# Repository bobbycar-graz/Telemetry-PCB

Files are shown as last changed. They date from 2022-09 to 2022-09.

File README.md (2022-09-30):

# Bobby-Car Telemetry PCB

This board should be mounted on the Bobby-Car.

There are 2 CAN bus connectors, pin-compatible with the boardcomputer PCB, and can either be wired:
- after the boardcomputer or
- in-line between the motorcontrollers and the boardcomputer

### Hardware Features
- SN65HVD230 CAN transceiver
- ESP32-WROOM-32E (8MB)
- CH343G USB to UART converter for programming
- ATGM336H-5N31 GNSS
  - supports GPS (US), GLONASS (Russia), Galileo (EU), BeiDou (China), QZSS (Japan)
  - u.FL connector for active antenna 
  - protocol compatible with NEO-6M
  - optional 3V rechargeable battery for fast cold start
- self bomb microSD card slot
- LM75B temperature sensor
- RA-01SH 868MHz LoRa module with two antenna options:
  - integrated u.FL connector for external helical antenna
  - solder jumper to enable the onboard PCB helical antenna
- TPMP2359DJ DC-DC converter (up to 30V input, 3.3V output), so board can be powered by:
  - USB-C connector (5V) or
  - CAN bus (12V-15V)
- TTL UART receive to receive log messages from the boardcomputer

### Use cases
- Acquire data with onboard sensors and send it to the boardcomputer
  - GPS/GNSS time, position, speed, heading
  - temperature
- Log data to the microSD card:
   - GPS and temperature data
   - CAN BUS messages
   - LoRa messages
   - ESP-NOW messages
   - GPS-mapped Wi-Fi scan results
   - UART log messages from the boardcomputer
- GPS geofencing (slowdown/stop, notification to other Bobby-Cars)
- Calibrate wheel circumference by comparing GPS speed with wheel speed
- Send GPS position over LoRa so that:
  - other Bobby-Cars can show nearby Bobby-Cars on a radar display
  - the Bobby-Car can be tracked on a map in case of loss or theft
- Control actuators such as door openers, lights, etc. over LoRa
- Receive LoRa messages from environmental sensors such as weather stations, air quality sensors, etc.
- Send ESP-NOW beacons with the current UTC time to other Bobby-Cars that lack a GNSS receiver
- Upload microSD card data to a cloud service automatically when connected to a Wi-Fi network

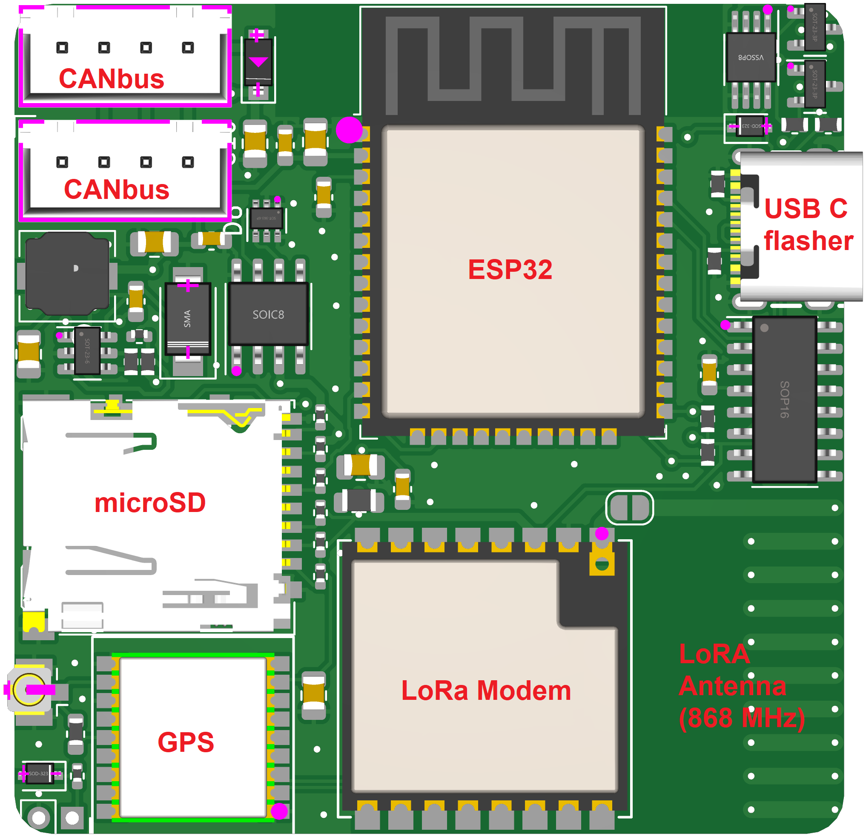
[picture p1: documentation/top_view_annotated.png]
PCB image


### Compliance
- Compliant with RED Directive 2014/53/EU (Radio Equipment Directive)
- Wi-Fi 2.4GHz 802.11b/g/n certified by Wi-Fi Alliance
- FCC ID of ESP32-WROOM-32E: [2AC7Z-ESP32WROOM32E](https://fccid.io/2AC7Z-ESP32WROOM32E)
- Compliant with LVD Directive 2014/35/EU (Low Voltage Directive)
- Compliant with EMC standard EN 55032, EN 55024, EN 61000-6-2, EN 61000-6-4 (Class B)
- Compliant with RoHS Directive 2011/65/EU (Restriction of Hazardous Substances)
- Compliant with REACH Regulation (EC) No 1907/2006 (Registration, Evaluation, Authorisation and Restriction of Chemicals)
- Compliant with WEEE Directive 2012/19/EU (Waste Electrical and Electronic Equipment)
- Compliant with ELV Directive 2011/65/EU (End of Life Vehicle)
- Compliant with ISO 11898-1:2003 CAN bus physical layer and data link layer specifications

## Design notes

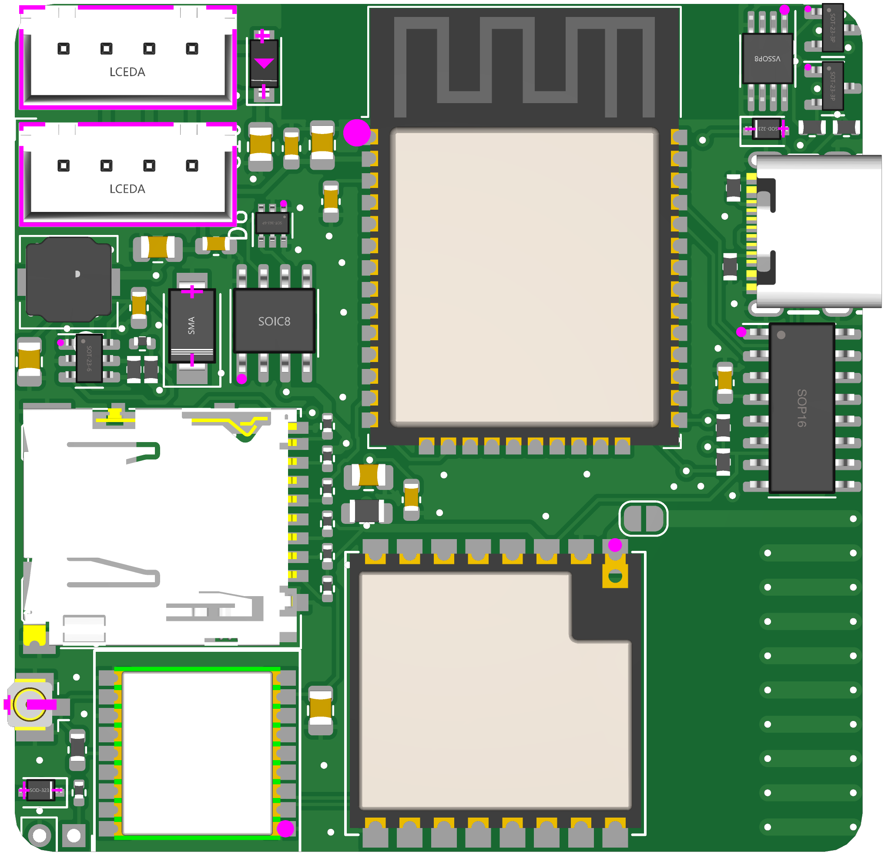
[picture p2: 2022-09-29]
documentation/top_view.png

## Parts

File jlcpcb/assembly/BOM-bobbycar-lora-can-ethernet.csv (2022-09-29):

Comment | Designator | Footprint | LCSC
bead | L2 | L_0805_2012Metric | C1017
Micro_SD_Card_Det_Hirose_DM3AT | J4 | microSD_HC_Hirose_DM3AT-SF-PEJM5 | C114218
SN65HVD231 | U6 | SOIC-8_3.9x4.9mm_P1.27mm | C12084
MC-311D | USBC1 | USB-C-SMD_MC-311D | C136423
Conn_01x04 | J1,J2 | JST_XH_B4B-XH-A_1x04_P2.50mm_Vertical | C144395
100n | C13,C3,C5,C6,C8 | C_0603_1608Metric | C14663
10uF | C1,C12,C4,C7 | C_0805_2012Metric | C15850
D_Schottky | D1,D2 | D_SOD-323 | C191023
1k | R15 | R_0402_1005Metric | C21190
SS8050_C2150 | Q1,Q2 | SOT-23 | C2150
B230A | D4 | D_SMA | C22452
12k | R10,R9 | R_0402_1005Metric | C22790
75k | R24 | R_0402_1005Metric | C23184
5k1 | R12,R8 | R_0402_1005Metric | C23186
470 | R1 | R_0402_1005Metric | C25117
24k | R25 | R_0402_1005Metric | C25769
47k | R16,R17,R18,R19,R20,R21 | R_0402_1005Metric | C25792
10k | R13,R14 | R_0402_1005Metric | C25804
Ai-Thinker-Ra-01SH | U2 | Ai-Thinker-Ra-01-LoRa | C2764087
LM75B | U3 | MSOP-8_3x3mm_P0.65mm | C2837470
CH343G | U5 | SOIC-16_3.9x9.9mm_P1.27mm | C2844153
MPM2359 | U7 | SOT-23-6 | C2959845
6.8nH | L1 | L_0603_1608Metric | C316305
4.7uH | L3 | L_Wuerth_HCI-5040 | C354606
10uF | C10,C9 | C_0805_2012Metric | C440198
10n | C11 | C_0603_1608Metric | C57112
ESP32-WROOM-32E | U1 | ESP32-WROOM-32 | C701342
D | D3 | D_SOD-123 | C8598
Antenna_Shield | AE1 | U.FL_Hirose_U.FL-R-SMT-1_Vertical | C88374
ATGM336H-5N31 | J3 | ATGM336H-5N31 | C90770
SP0505BAJT | D6 | SOT-363_SC-70-6 | SMF05CT1G
Battery_Cell | BT1 | PinSocket_1x02_P2.00mm_Vertical
Jumper_2_Open | JP1 | SolderJumper-2_P1.3mm_Open_RoundedPad1.0x1.5mm
Antenna | AE2 | Texas_SWRA416_868MHz_915MHz

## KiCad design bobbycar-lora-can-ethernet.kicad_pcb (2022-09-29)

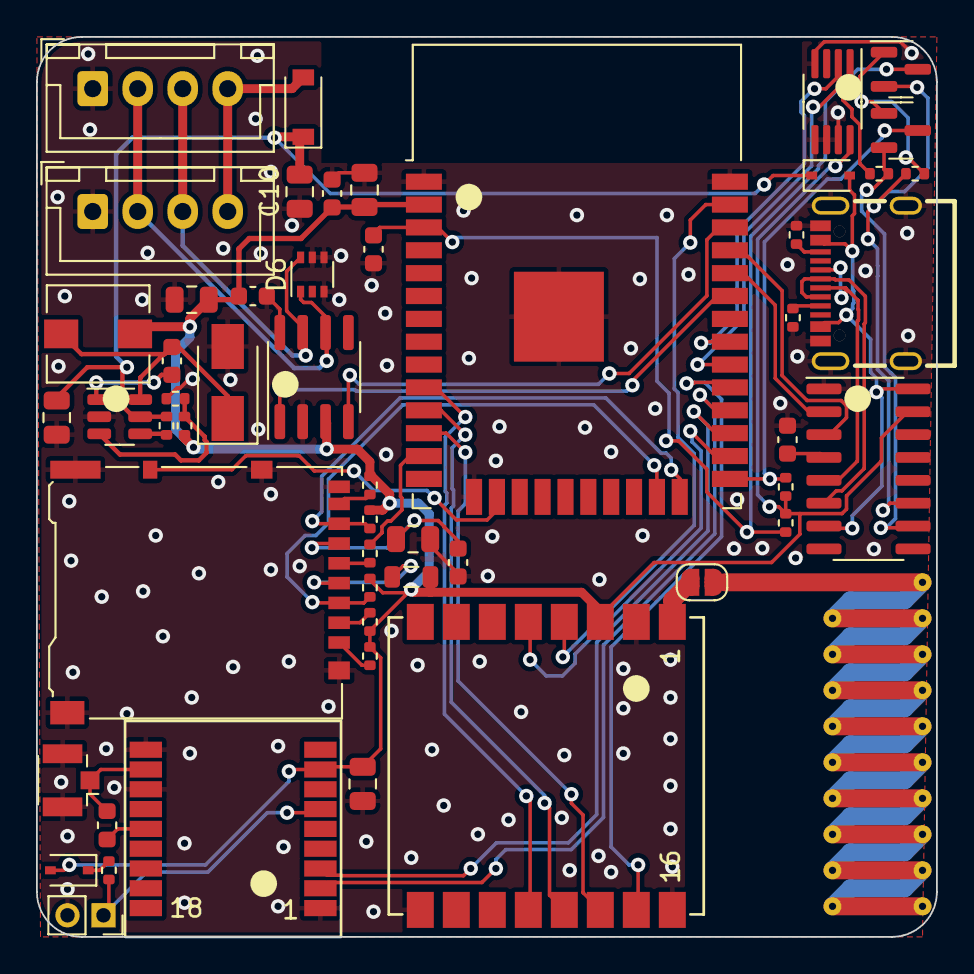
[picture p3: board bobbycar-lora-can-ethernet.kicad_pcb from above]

Board: 2 copper layers, 50.0 x 50.0 mm, 53 parts (0 on the bottom side), 52 nets.

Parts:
AE1: Antenna_Shield; U.FL_Hirose_U.FL-R-SMT-1_Vertical
AE2: Antenna; Texas_SWRA416_868MHz_915MHz
BT1: Battery_Cell; PinSocket_1x02_P2.00mm_Vertical
C1, C7, C9, C10, C12: 10uF; C_0805_2012Metric
C3, C5, C6, C8, C13: 100n; C_0603_1608Metric
C4: 10u; C_0805_2012Metric
C11: 10n; C_0603_1608Metric
D1, D2: D_Schottky; D_SOD-323
D3: D; D_SOD-123
D4: B230A; D_SMA
D6: SP0505BAJT; SOT-363_SC-70-6
J1, J2: Conn_01x04; JST_XH_B4B-XH-A_1x04_P2.50mm_Vertical
J3: ATGM336H-5N31
J4: Micro_SD_Card_Det_Hirose_DM3AT; microSD_HC_Hirose_DM3AT-SF-PEJM5
JP1: Jumper_2_Open; SolderJumper-2_P1.3mm_Open_RoundedPad1.0x1.5mm
L1: 6.8nH; L_0603_1608Metric
L2: bead; L_0805_2012Metric
L3: 4.7uH; L_Wuerth_HCI-5040
Q1, Q2: SS8050_C2150; SOT-23
R1: 470; R_0402_1005Metric
R8, R12: 5k1; R_0402_1005Metric
R9, R10: 12k; R_0402_1005Metric
R13, R14: 10k; R_0402_1005Metric
R15: 1k; R_0402_1005Metric
R16, R17, R18, R19, R20, R21: 47k; R_0402_1005Metric
R24: 75k; R_0402_1005Metric
R25: 24k; R_0402_1005Metric
U1: ESP32-WROOM-32E; ESP32-WROOM-32
U2: Ai-Thinker-Ra-01SH; Ai-Thinker-Ra-01-LoRa
U3: LM75B; MSOP-8_3x3mm_P0.65mm
U5: CH343G; SOIC-16_3.9x9.9mm_P1.27mm
U6: SN65HVD231; SOIC-8_3.9x4.9mm_P1.27mm
U7: MPM2359; SOT-23-6
USBC1: MC-311D; USB-C-SMD_MC-311D

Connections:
15V: C9.2, C10.2, D2.1 (K), D3.1 (K), R15.2, U7.5 (IN)
+3V3: C1.1, C4.2, C5.2, C8.1, C12.2, D1.2 (A), J3.8, L2.1, L3.2, R13.1, R14.2, R16.1, R17.1, R18.1, R20.1, R21.1, R24.2, U1.2 (VDD), U2.3 (VDD), U3.8 (+Vs), U5.15 (VIO), U6.3 (VCC)
+5V: D2.2 (A), U5.7 (VBUS), U5.16 (VDD5), USBC1.A4-B9 (VBUS), USBC1.B4-A9 (VBUS)
CANH: D6.6 (K), J1.3, J2.3, U6.7 (CANH)
CANL: D6.1 (K), J1.2, J2.2, U6.6 (CANL)
CAN_RX: U1.36 (IO22), U6.4 (R)
CAN_TX: U1.33 (IO21), U6.1 (D)
DTR: Q2.2 (E), R9.1, U5.10 (~DTR/TNOW)
EN: C13.2, Q1.3 (C), R13.2, U1.3 (EN)
ESP_RX: U1.34 (RXD0/IO3), U5.2 (TXD)
ESP_TX: U1.35 (TXD0/IO1), U5.3 (RXD)
GND: AE1.2 (Shield), BT1.2 (-), C1.2, C3.1, C4.1, C5.1, C6.1, C7.2, C8.2, C9.1, C10.1, C12.1, C13.1, D4.2 (A), D6.3 (K), D6.4 (K), D6.5 (K), J1.1, J2.1, J3.1, J3.10, J3.12, J4.9 (DET_B), J4.11 (SHIELD), R8.2, R12.1, R25.1, U1.1 (GND), U1.15 (GND), U1.38 (GND), U1.39 (GND), U2.2 (GND), U2.9 (GND), U2.16 (GND), U3.4 (GND), U3.5 (A2), U3.6 (A1), U3.7 (A0), U5.1 (GND), U6.2 (GND), U6.8 (Rs), U7.2 (GND), USBC1.1 (SHIELD), USBC1.2 (SHIELD), USBC1.3 (SHIELD), USBC1.4 (SHIELD), USBC1.A1-B12 (GND), USBC1.B1-A12 (GND)
GPIO2_SD_DAT0: J4.7 (DAT0), R20.2, U1.24 (IO2)
GPIO14_SD_CLK: R19.1, U1.13 (IO14)
GPIO15_SD_CMD: J4.3 (CMD), R18.2, U1.23 (IO15)
GPS_RX: J3.3, U1.27 (IO16)
GPS_TX: J3.2, U1.28 (IO17)
I2S_SCL: U1.31 (IO19), U3.2 (SCL)
I2S_SDA: U1.30 (IO18), U3.1 (SDA)
IO0: Q2.3 (C), R14.1, U1.25 (IO0)
LORA_CLK: U1.10 (IO25), U2.12 (SCK)
LORA_MISO: U1.11 (IO26), U2.13 (MISO)
LORA_MOSI: U1.12 (IO27), U2.14 (MOSI)
LORA_NSS: U1.29 (IO5), U2.15 (~NSS)
LORA_RESET: U1.37 (IO23), U2.4 (~RESET)
LORA_TX_EN: U1.26 (IO4), U2.5 (DIO0)
unnamed: AE1.1 (A), J3.11, L1.1
unnamed: AE2.1 (A), JP1.2 (B)
unnamed: C3.2, U5.4 (V3)
unnamed: C6.2, C7.1, J4.6 (VSS)
unnamed: C11.1, D4.1 (K), L3.1, U7.6 (SW)
unnamed: C11.2, U7.1 (BST)
unnamed: D1.1 (K), R1.1
unnamed: D3.2 (A), J1.4, J2.4
unnamed: J3.14, L1.2
unnamed: J4.1 (DAT2), R16.2
unnamed: J4.2 (DAT3/CD), R17.2
unnamed: J4.4 (VDD), L2.2
unnamed: J4.5 (CLK), R19.2
unnamed: J4.8 (DAT1), R21.2
unnamed: JP1.1 (A), U2.1 (ANT)
unnamed: Q1.1 (B), R9.2
unnamed: Q2.1 (B), R10.2
unnamed: R8.1, USBC1.A5 (CC1)
unnamed: R12.2, USBC1.B5 (CC2)
unnamed: R15.1, U7.4 (EN)
unnamed: R24.1, R25.2, U7.3 (FB)
RTS: Q1.2 (E), R10.1, U5.11 (~RTS)
SD_DETECT: J4.10 (DET_A), U1.16 (IO13)
USB_DN: U5.6 (UD-), USBC1.A7 (DN1), USBC1.B7 (DN2)
USB_DP: U5.5 (UD+), USBC1.A6 (DP1), USBC1.B6 (DP2)
VBAT_3V: BT1.1 (+), J3.6, R1.2

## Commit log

2022-09-29 initial order on jlcpcb
    [BOM-bobbycar-lora-can-ethernet.csv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]
2022-09-30 improve README, add component number in schematics
    [bobbycar-lora-can-ethernet.kicad_sch]
